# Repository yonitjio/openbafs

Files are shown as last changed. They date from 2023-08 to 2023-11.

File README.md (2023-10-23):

# Basic Automatic Filament Switch

BAFS is a kind of multi material unit for 3d printer. It's very basic, don't expect fancy stuff. It only do one thing: switching filament.

Features:

1. Modular design, i.e. you decide how many ports you want, print accordingly.
2. Only 1 pwm port needed from the printer
3. Redundant design, if one of the motor port stop working, most likely it won't affect the other.
4. Cheap, it uses commonly available parts.
5. Easy to print, for the most parts, you might not need to print with support at all.

BAFS is a great and affordable way to learn and understand how multi filament / multi material 3d printing works.

Be aware this design has the same problems/challenges as similar design using single nozzle and y-splitter: jams, clogging, color bleeds, etc.

To use BAFS you need firmware support, unfortunately, currently there's no official firmware support.

See my other repo for custom firmware:
* Marlin: [openbafs-marlin](https://github.com/yonitjio/openbafs-marlin).
* Klipper: [openbafs-klipper](https://github.com/yonitjio/openbafs-klipper).

Most printers don't have many servo ports, to solve this, I use arduino, stepper motor shield and custom board. There are two variants (branch) regarding communication between printer and bafs:

PWM (Main Branch):
One pwm port from the printer to generate pwm pulse that signal which port to use to external module.

Serial (Sc Branch):
Serial port from the printer to command the external module.

Non printed parts:

- Servos (I use MG996R)
- A Stepper motor (for direct drive printers)
- M5 rod, stainless is preferable.
- M5 to M5 coupler
- M3 bolts and nuts
- M4 bolts
- Long M4 bolts and nuts
- Bearings 625zz, 623zz, u604zz
- Extruder gears
- Grease
- PC4-M6

Electronic parts:

- Arduino
- Protoshield for Arduino
- Stepdown module
- Power Supply
- Connectors
- Wires
- Connectors

These parts are only for the switch, you still need at least a y-splitter. Use whichever work for you. You can search it on thingiverse, printables, etc.

For y-splitter you can try this:
https://www.printables.com/model/488193-4-to-1-bowdenptfe-tube-joinersplitter-stronger-bas

### Extrusion System
Initially BAFS was designed for bowden system, but since I changed my printer to direct drive, I also update BAFS to support direct drive.

With bowden extrusion system, BAFS also acts as the extruder, it uses the printer's stepper motor.

For printers with direct drive extrusion system, it acts as a feeder. It needs additional stepper motor.

Each version requires different firmware. Other than the stepper motor and firmware, everything else is the same.

This repo is for direct drives.

### Electronics
To build the electronics you need to have at least basic skills about arduino and electronics. It requires soldering and making wires with connectors.

It is pretty straight forward. Nothing fancy here. You just need to connect the servos, stepper motor and the printer to arduino.

There are plenty tutorials about using servos and stepper motor with arduino.

Adjust the codes according to your setup.

#### DISCLAIMER:
This is an experimental project. It may or may not work. Use it at your own risk.

#### Notes:
- Even though it's modular, it's better to plan ahead to minimize costs, for example if you plan to use 4 filaments but want to start with 2 first, it's better to prepare the shaft and bolts for 4 filaments from the start. This is because the you need longer shaft and bolts for more ports for the filaments.
- Values in the code are for my setup. Most likely it won't work for yours. Adjust accordingly first.
- If you decided to use this with Klipper, you don't need the software part from this repo.
- Branch SV is for pwm, SC is for serial.
- Refer to [wiki](https://github.com/yonitjio/openbafs/wiki) for more detail.
- If you'd like to buy me a coffee or a tool or supplies for this project, or you want to read more, click here:

  "Buy Me A Coffee" (https://www.buymeacoffee.com/yonitjio)

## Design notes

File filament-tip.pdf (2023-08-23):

Important points in making good filament p:

### 1. Printer Tuning

Tuned printer makes everything easier, at the very least, tuned the e-steps, extrusion mulplier and temperature.

Temperature is the most important factor
Changing the temperature most likely means changing everything else. Use PID or MPC for stable temperature.

Print Temp Tower, choose the lowest possible temp. Usually, it’s easier to make good filament p on lower temp.

### 2. Pressure inside the nozzle

Traveling from print object to wipe toper reduce the pressure inside nozzle. The amount of pressure lost while traveling depends on the distance, ideally this informaon can be calculated and made into formula. I don’t have the skill to do that.

Also, unless the printed model is very simple, most likely the distance/pressure lost varies even between layers on the same object.

Prusa Slicer a.empts to address this with extruding some amount of filament to wipe tower, but somemes it’s not enough.
If necessary, make a straight line on the beginning of the ramming parameter.

### 3. Ramming

The purpose of ramming is to push filament into the nozzle in a way that the melng plasc inside the nozzle isn’t carried away when unloading. Ramming usually requires larger volume than the volume to stabilize pressure.

In other words, we are trying to overwhelm the nozzle melng capabilies, which then, hopefully, when the unloading begins, only the un-melted part of the filament is pulled out.

### 4. Resng

Somemes, it helps to give some resng period. The resng period will allow the filament to melt even more, resulng less string.

### 5. Unloading

Speed plays a big role in making good filament p. Too slow, the effect of ramming is lost. Too fast, the ramming result is not set yet. Both will not produce a good filament p. Start with the default value first (100 mm/s), adjust if needed.

### 6. Cooling

Cooling means that the filament is moved forward and backward for somemes, allowing it to cool down and become hard again. Some filament needs more me to become hard again than other filament.

This is important for Direct Drive system where the filament is parked before the extruder. So: filament will be deformed by the extruder gear which then can cause jamming.

Troubleshoong:

- Thick string / Blunt p
- Not enough me to melt the filament
- Volume too high
- Temperature too low

Soluon:

- Increase the me
- Lower the volumetric speed.
- Increase temperature
- Ripped p
- Unloading speed to fast
- Volume too high

Soluon:

- Lower unloading speed
- lower volumetric speed.
- Smooth, long p
- Not enough volume
- Time is too long
- Temperature too high

Soluon:

- Increase volumetric speed
- Lower me
- Lower temperature
- Use cooling moves
- Inconsistent filament p
- Extruder problem
- Heat creep
- Temperature too high
- Wrong slicer seAng

Soluon:

- Tune the printer
- Check slicer seAngs

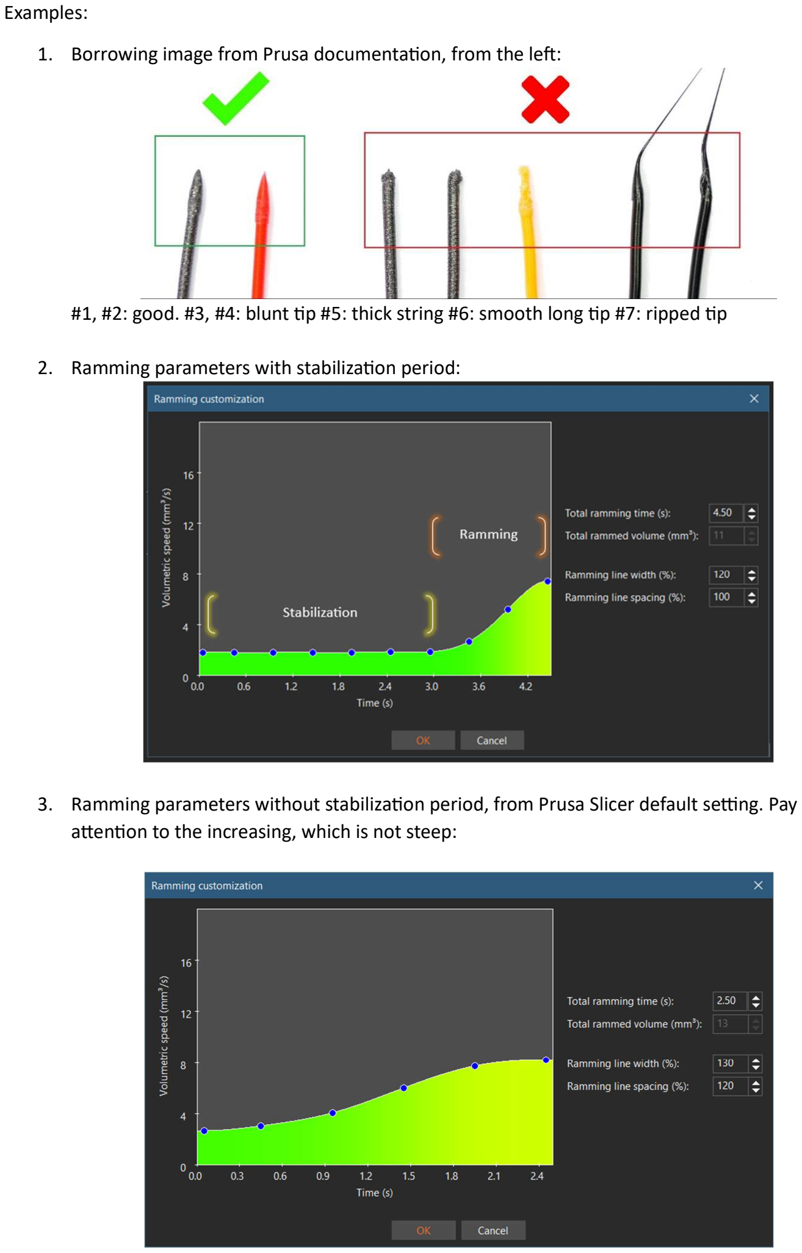
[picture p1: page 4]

Examples:

### 1. Borrowing image from Prusa documentaon, from the le::

#1, #2: good. #3, #4: blunt p #5: thick string #6: smooth long p #7: ripped p

### 2. Ramming parameters with stabilizaon period:

### 3. Ramming parameters without stabilizaon period, from Prusa Slicer default seAng. Pay

a.enon to the increasing, which is not steep:

### 4. Effects of ramming with v6 clone, 0.4 nozzle, 190oC, custom direct drive:

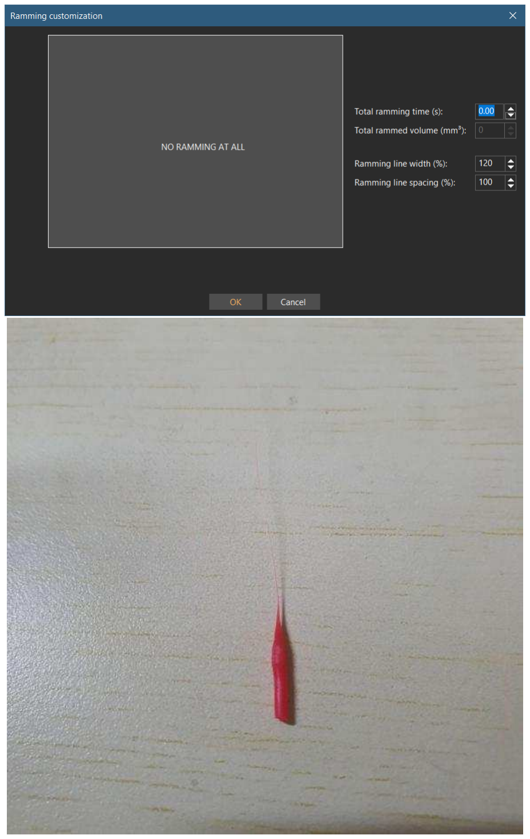
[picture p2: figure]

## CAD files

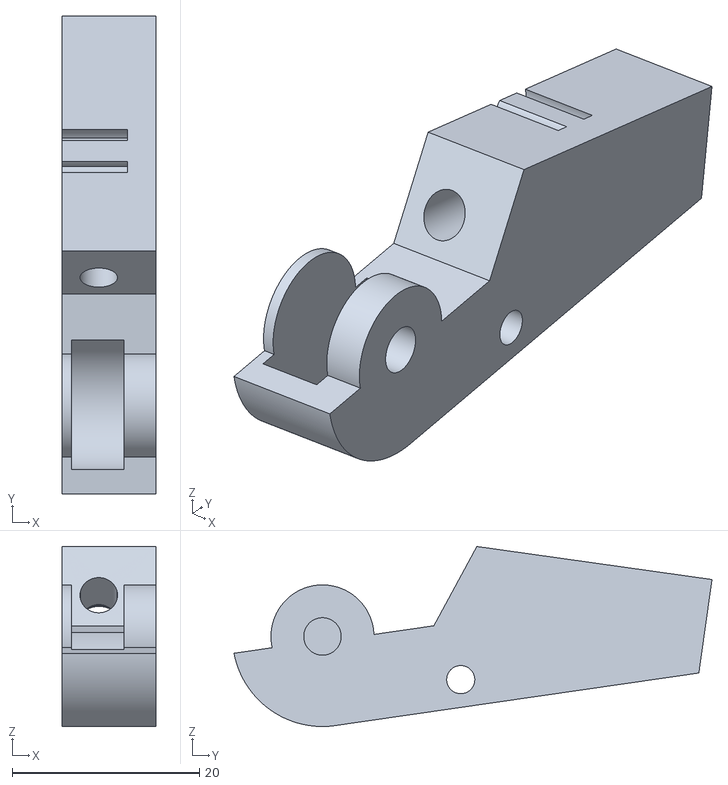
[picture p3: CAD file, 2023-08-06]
prints/Extruder Arm Even.stl
10.0 x 51.0 x 19.2

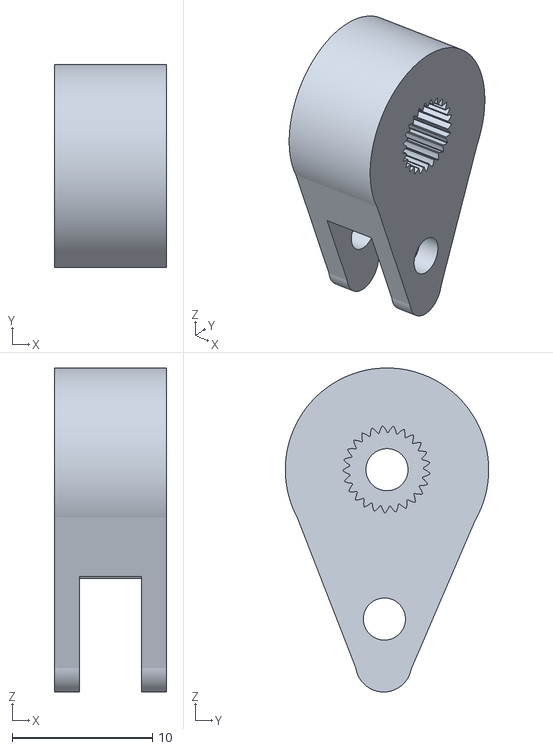
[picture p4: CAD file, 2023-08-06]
prints/Servo Knuckle.stl
8.00 x 14.5 x 23.1

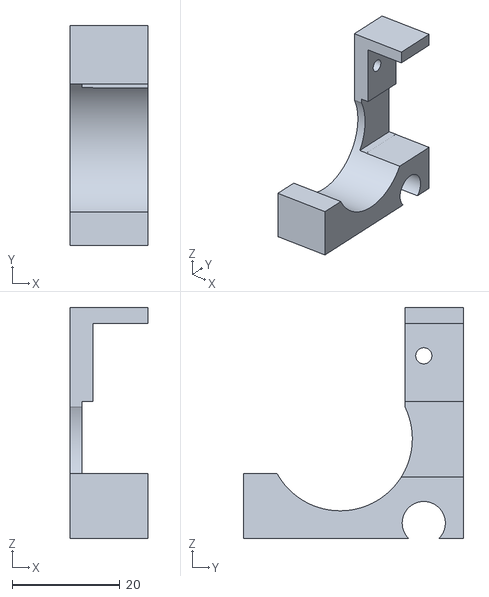
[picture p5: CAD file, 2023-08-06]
prints/Cover Odd.stl
14.4 x 40.8 x 42.9

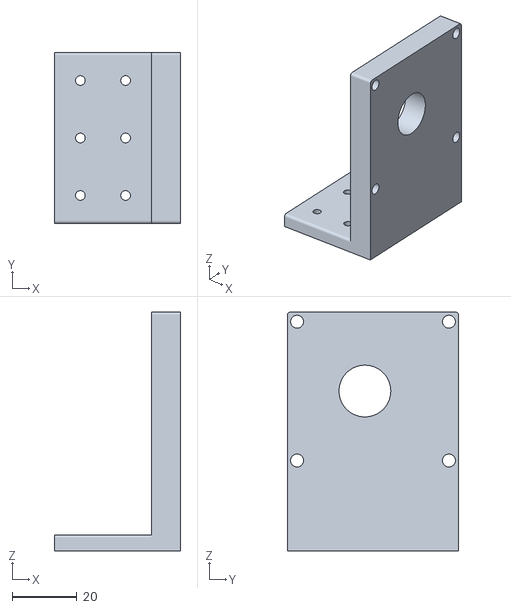
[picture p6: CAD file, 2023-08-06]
prints/End Block.stl
39.0 x 53.0 x 74.0

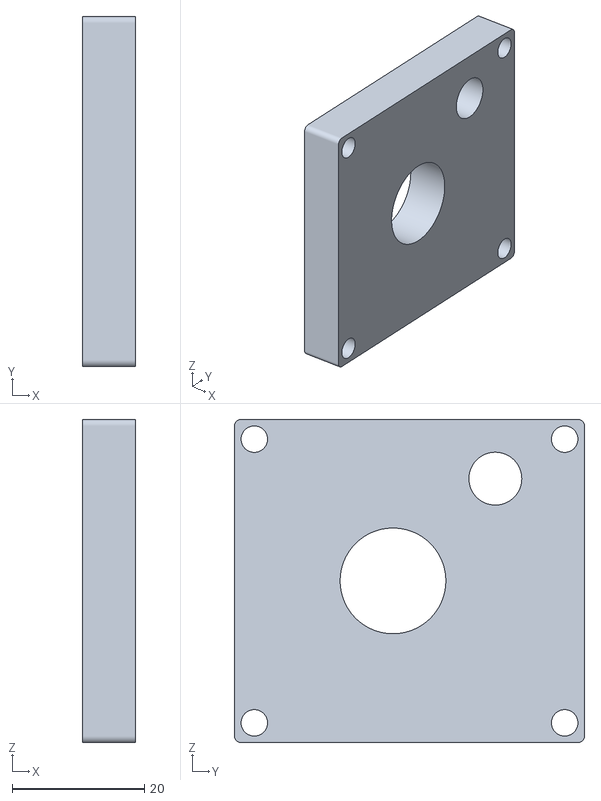
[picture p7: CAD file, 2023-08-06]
prints/Spacer.stl
8.00 x 53.0 x 49.0

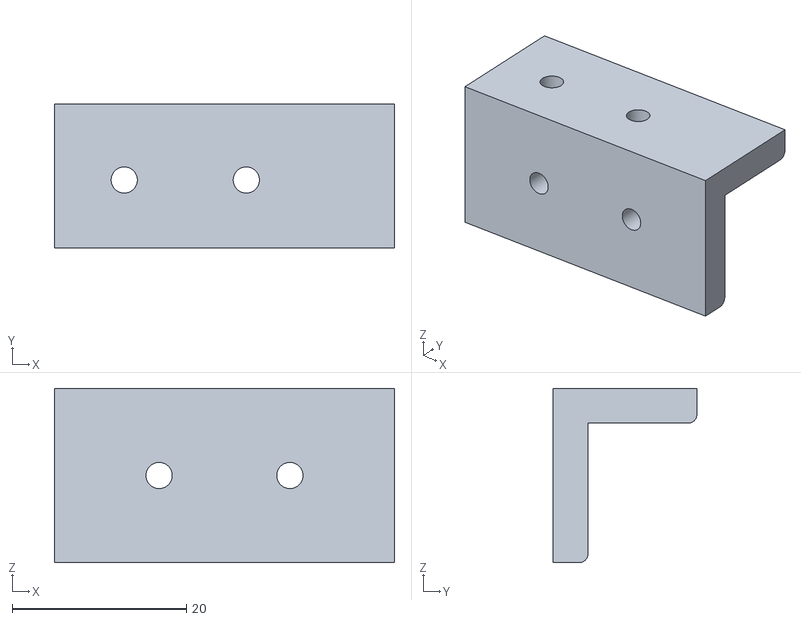
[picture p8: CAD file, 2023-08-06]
prints/End Bracket Bottom.stl
39.0 x 16.5 x 20.0

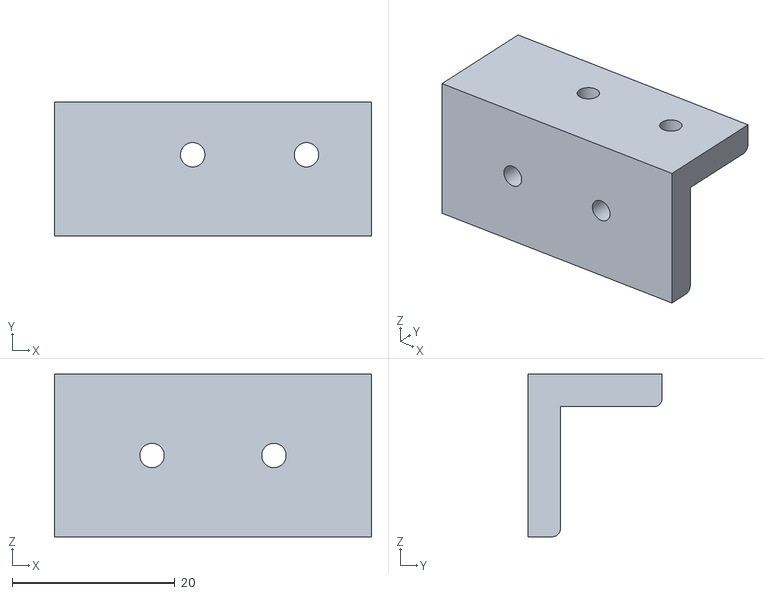
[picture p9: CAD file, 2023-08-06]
prints/Start Bracket Bottom.stl
39.0 x 16.5 x 20.0

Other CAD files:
prints/End Bracket Top.stl
prints/Start Bracket Top.stl
prints/Cover Even.stl
prints/Extruder Arm Odd.stl

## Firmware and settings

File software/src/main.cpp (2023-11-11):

#define SERVOINPUT_SUPPRESS_WARNINGS

#include <SPI.h>
#include <Wire.h>
#include <Adafruit_PWMServoDriver.h>
#include <SoftwareSerial.h>
#include <GCodeParser.h>
#include "Stepper.h"

#define SERVO_CNT 4
#define SERVO_SDA_PIN 4
#define SERVO_SCL_PIN 5
#define SERVO_MIN_MS 600
#define SERVO_MAX_MS 2400
#define SERVO_FREQ 50 // Analog servos run at ~50 Hz updates
#define SERVO_OSC_FREQ 25800000

#define STEPPER_EN_PIN 9
#define STEPPER_STEP_PIN 10
#define STEPPER_DIR_PIN 11
#define SMALL_FEED_DISTANCE 5

// Stepper
const byte micro_step = 16;
const int step_rotation = 200;
const int dist_rotation = 34.56;

const int retract_distance[] = {107, 107, 107, 107};
const int feed_distance[] = {120, 120, 120, 120};
const int slower_margin[] = {10, 10, 10, 10};

float step_accelleration = 40000;
float step_speed = 40000;
float step_max_speed = 40000;
float step_slower_speed = 1000;

// speed is steps/second
// 1.8deg stepper => 200 steps/revolution, 16 microsteps => 3200 steps/rev
// mk8 brass gear diameter => 11mm
// 1 revolution => 34.56mm
// speed 4000 steps/sec => 1000/3200 rev/sec = 0.3125 rev/sec => 0.3125 * 34.56 mm/sec = 10.8 mm/sec
// speed 12000 steps/sec => 12000/3200 = 3.75 rev/sec => 3.75 * 34.56 mm/sec = 129.6 mm/sec

Stepper stepper(AccelStepper::DRIVER, STEPPER_STEP_PIN, STEPPER_DIR_PIN);

// #define DEBUG
// #define DEBUG_SELECTION
#define DEBUG_PRINTER_SERIAL
#define DEBUG_GCODE
// #define DEBUG_STEPPER

// Filament Sensor
#define FILAMENT_SENSOR_PIN 2

// Camera Remote
#define CAM_PIN 3
#define CAM_IDLE 305000
unsigned long cam_last_active = millis();

// Software Serial
#define SERIAL_RX_PIN 12
#define SERIAL_TX_PIN 13

SoftwareSerial printer_serial(SERIAL_RX_PIN, SERIAL_TX_PIN); // RX, TX
GCodeParser GCode = GCodeParser();

int selection = -1;
int last_selection = -1;

int mode = 0; //0: operational, 1: configure, 2: default serial as gcode receiver

// Servo
Adafruit_PWMServoDriver servoController = Adafruit_PWMServoDriver();

const byte servo_on_deg[] = {14, 162, 32, 152};
const byte servo_off_deg[] = {90, 90, 90, 90};

String input_string;

void onRising();
void processPWM();
void switchFilament();
void feedFilament();
String getValue(String data, char separator, int index);
int mapSelection(int s);
int getFeedDistance(int sel);
int getSmallFeedDistance(int sel);
int getSlowerMargin(int sel);
int getRetractDistance(int sel);
void triggerCamera();
void wakeupBluetooth();
void servoWrite(uint8_t i, uint16_t value);
void servoOff(uint8_t i);
void servoOn(uint8_t i);

void setup() {
  Serial.begin(9600);

  // Stepper
  stepper.setEnablePin(STEPPER_EN_PIN);
  stepper.setPinsInverted(true, false, true);
  stepper.setMinPulseWidth(1);

  stepper.setAcceleration(step_accelleration);
  stepper.setMaxSpeed(step_max_speed);
  stepper.setSpeed(step_speed);

  stepper.setMicroStep(micro_step);
  stepper.setDistancePerRotation(dist_rotation);
  stepper.setStepsPerRotation(step_rotation);

  // Servo
  servoController.begin();
  servoController.setOscillatorFrequency(SERVO_OSC_FREQ);
  servoController.setPWMFreq(SERVO_FREQ);
  delay(10);

  // Filament Sensor
  pinMode(FILAMENT_SENSOR_PIN, INPUT_PULLUP);

  // Camera Remote
  pinMode(CAM_PIN, OUTPUT);
  digitalWrite(CAM_PIN, HIGH);
  cam_last_active = millis();

  // Printer Serial
  printer_serial.begin(9600);
  printer_serial.println("Ok");
}

void feedFilament(){
  servoOn(last_selection);
  delay(250);

  stepper.enableOutputs();
  stepper.setCurrentPosition(0);
  stepper.runRelative(getSmallFeedDistance(last_selection));
  stepper.setSpeed(step_speed);
  stepper.disableOutputs();
  delay(250);

  servoOff(last_selection);
  delay(250);
}

void switchFilament(){
  if (selection >= SERVO_CNT) {
    return;
  }

  if (last_selection != selection) {
    if (last_selection > -1) {
      stepper.enableOutputs();

      #ifdef DEBUG_SELECTION
        Serial.print(" Turning on "); Serial.print(last_selection); Serial.println(".");
      #endif

      servoOn(last_selection);
      delay(250);

      #ifdef DEBUG_STEPPER
        Serial.print(" Retracting: ");  Serial.print(last_selection); Serial.print(", "); Serial.print(retract_distance[last_selection]);
      #else
        Serial.print(" Retracting: "); Serial.println(last_selection);
      #endif

      stepper.setCurrentPosition(0);
      stepper.runRelative(-getRetractDistance(last_selection));
      stepper.setSpeed(step_speed);
      delay(250);

      #ifdef DEBUG_SELECTION
        Serial.print(" Turning off "); Serial.print(last_selection); Serial.println(".");
      #endif
      servoOff(last_selection);
      delay(250);

      #ifdef DEBUG_SELECTION
        Serial.print(" Turning on "); Serial.print(selection); Serial.println(".");
      #endif
      servoOn(selection);
      delay(250);

      #ifdef DEBUG_STEPPER
        Serial.print(" Feeding: "); Serial.print(selection); Serial.print(", "); Serial.print(feed_distance[selection]);
      #else
        Serial.print(" Feeding: "); Serial.println(selection);
      #endif

      stepper.setCurrentPosition(0);
      stepper.runRelative(getFeedDistance(selection) - getSlowerMargin(selection));
      stepper.setSpeed(step_slower_speed);
      stepper.runRelative(getSlowerMargin(selection));
      stepper.setSpeed(step_speed);
      delay(250);

      #ifdef DEBUG_SELECTION
        Serial.print(" Turning off "); Serial.print(selection); Serial.println(".");
      #endif

      servoOff(selection);
      delay(250);
    }

    last_selection = selection;

    stepper.disableOutputs();
  }
}

void wakeupBluetooth(){
  digitalWrite(CAM_PIN, LOW);
  delay(50);
  digitalWrite(CAM_PIN, HIGH);
  cam_last_active = millis();
}

void triggerCamera(int d){
  Serial.println("Triggering Camera");
  digitalWrite(CAM_PIN, LOW);
  delay(d);
  digitalWrite(CAM_PIN, HIGH);
  cam_last_active = millis();
}

void processGCode(){
  if (!GCode.blockDelete){
    if (GCode.HasWord('C')) { // C-Codes
      int cCodeNumber = (int)GCode.GetWordValue('C');
      #ifdef DEBUG_GCODE
        Serial.print(" C: "); Serial.print(cCodeNumber); Serial.println(".");
      #endif
      switch (cCodeNumber){
        case 0: { // feed a little bit of filament
          feedFilament();
          if (mode == 0)
            printer_serial.println("ok");
          else
            Serial.println("ok");
        }
        break;
        default: {
            Serial.println(" Unknown C code.");
        }
        break;
      }
    } else if (GCode.HasWord('M')) { // M-Codes
      int mCodeNumber = (int)GCode.GetWordValue('M');
      #ifdef DEBUG_GCODE
        Serial.print(" M: "); Serial.print(mCodeNumber); Serial.println(".");
      #endif
      switch (mCodeNumber){
        case 709: { // Reset
          selection = -1;
          last_selection = -1;
          mode = 0;
          #ifdef DEBUG_GCODE
            Serial.println("BAFSD Reset.");
          #endif
        }
        break;
        case 412: { // Check filament
          int state = digitalRead(FILAMENT_SENSOR_PIN);
          #ifdef DEBUG_GCODE
            Serial.print(" Filament: "); Serial.print(state); Serial.println(".");
          #endif
          if (state == LOW){  // low = filament present, high = filament not present
            if (mode == 0)
              printer_serial.println("ok");
            else
              Serial.println("ok");
          } else {
            if (mode == 0)
              printer_serial.println("no");
            else
              Serial.println("no");
          }
        }
        break;
        case 240: { // Camera
          int duration = (int)GCode.GetWordValue('D');
          triggerCamera(duration);
        }
        break;
        default: {
            Serial.println(" Unknown M code.");
        }
        break;
      }
    } else if (GCode.HasWord('T')) { // T-Codes
      int tCodeNumber = (int)GCode.GetWordValue('T');
      #ifdef DEBUG_GCODE
        Serial.print(" T: "); Serial.print(tCodeNumber); Serial.println(".");
      #endif
      selection = tCodeNumber;
      switchFilament();
      if (mode == 0)
        printer_serial.println("ok");
      else
        Serial.println("ok");
  }
  }
}

void loop() {
  unsigned long now = millis();
  if (now - cam_last_active > CAM_IDLE) {
    wakeupBluetooth();
  }
  if (mode == 0) {
    if (printer_serial.available()) {
      if (GCode.AddCharToLine(printer_serial.read())) {
        #ifdef DEBUG_PRINTER_SERIAL
          Serial.print(" Received: "); Serial.println(GCode.line);
        #endif
        GCode.ParseLine();
        processGCode();
      }
    }
  }
  else if (mode == 2) {
    if (Serial.available()) {
      if (GCode.AddCharToLine(Serial.read())) {
        #ifdef DEBUG_PRINTER_SERIAL
          Serial.print(" Received: "); Serial.println(GCode.line);
        #endif
        GCode.ParseLine();
        processGCode();
      }
    }
    return;
  }

  String command = "";
  if (Serial.available() > 0) {
    String input_string = Serial.readStringUntil('\n');
    input_string.trim();
    Serial.println("Received: " + input_string);
    if (input_string.equalsIgnoreCase("m0")) {
      mode = 0;
      // Servo
      for(int n = 0; n < SERVO_CNT; n++)
      {
        servoOff(n);
        delay(250);
      }
      Serial.println("Entering M0 mode.");
    } else if (input_string.equalsIgnoreCase("m1")) {
      mode = 1;
      Serial.println("Entering M1 mode.");
    } else if (input_string.equalsIgnoreCase("m2")) {
      mode = 2;
      Serial.println("Entering M2 mode.");
    } else if (input_string.equalsIgnoreCase("rs")) {

      double pulselength;
      pulselength = 1000000; // 1,000,000 us per second

      uint16_t prescale = servoController.readPrescale();

      prescale += 1;
      pulselength *= prescale;
      pulselength /= SERVO_OSC_FREQ;

      uint16_t pwm = servoController.getPWM(selection);
      uint16_t pulse = pwm * pulselength;

      unsigned long camIdle = millis() - cam_last_active;

      Serial.print(" Mode: "); Serial.println(mode);
      Serial.print(" Selection: "); Serial.println(selection);
      Serial.print(" pwm: "); Serial.println(pwm);
      Serial.print(" pulse: "); Serial.println(pulse);
      Serial.print(" pulseLength: "); Serial.println(pulselength);
      Serial.print(" Cam Idle: "); Serial.println(camIdle);

      if (pulse < SERVO_MIN_MS) {
        pulse = SERVO_MIN_MS;
      }

      if (pulse > SERVO_MAX_MS) {
        pulse = SERVO_MAX_MS;
      }
      uint16_t deg = map(pulse, SERVO_MIN_MS, SERVO_MAX_MS, 0, 180);

      Serial.print(" deg: "); Serial.println(deg);
      Serial.print(" filament: "); Serial.println(digitalRead(FILAMENT_SENSOR_PIN));
      Serial.println();
    }else {
      command = input_string;
    }
  }
  if (mode == 1) {
    if (command.length() > 0){
      #ifdef DEBUG
        Serial.print("command: "); Serial.println(command);
      #endif

      char cmd = getValue(command, ' ', 0)[0];
      String p1 = getValue(command, ' ', 1);
      String p2 = getValue(command, ' ', 2);

      switch (cmd)
      {
        case 'c': // camera
          {
            int d_val = p1.toInt();
            triggerCamera(d_val);
          }
        break;
        case 'e': // small feed
          {
            long t = millis();
            feedFilament();
            t = millis() - t;
            Serial.print("time: "); Serial.println(t);
          }
          break;
        case 'f': // switch filament p1 selection
          {
            long t = millis();
            selection = p1.toInt();
            switchFilament();
            t = millis() - t;
            Serial.print("time: "); Serial.println(t);
          }
          break;
        case 'd': // move stepper p1 = steps
          {
            long step_val = p1.toInt();

            #ifdef DEBUG
              Serial.print("step_val: "); Serial.println(p1);
            #endif

            stepper.enableOutputs();
            stepper.move(step_val);
            stepper.runToPosition();
            stepper.setSpeed(step_speed);
            stepper.disableOutputs();
          }
          break;
        case 'p': // move stepper p1 = distance, p2 = not used
          {
            long dis_val = p1.toInt();
            long t = millis();
            #ifdef DEBUG
              Serial.print("dis_val: "); Serial.println(p1);
            #endif

            stepper.enableOutputs();
            stepper.setCurrentPosition(0);
            #ifdef DEBUG
              long steps = stepper.runRelative(dis_val);
            #else
              stepper.runRelative(dis_val);
            #endif
            stepper.setSpeed(step_speed);
            stepper.disableOutputs();

            t = millis() - t;
            #ifdef DEBUG
              Serial.print("steps: "); Serial.println(steps);
              Serial.print("time: "); Serial.println(t);
            #endif
          }
          break;
        case 'm': // select servo p1 = servo
          {
            int s_val = p1.toInt();

            #ifdef DEBUG
              Serial.print("s_val: "); Serial.println(p1);
            #endif

            s_val = constrain(s_val, 0, SERVO_CNT);
            last_selection = s_val;
            selection = s_val;
          }
          break;
        case 's': // set servo degree p1 = servo index, p2 = degree
          {
            int s_val = p1.toInt();
            int d_val = p2.toInt();

            #ifdef DEBUG
              Serial.print("s_val: "); Serial.print(p1); Serial.print( " d_val: "); Serial.println(p2);
            #endif

            s_val = constrain(s_val, 0, SERVO_CNT);
            d_val = constrain(d_val, 0, 180);

            Serial.print("Moving "); Serial.println(s_val);
            servoWrite(s_val, d_val);
          }
          break;
        case 't': // test servos and stepper
          {
              for(int n = 0; n < SERVO_CNT; n++)
              {
                servoWrite(n, 100);
                delay(500);
                servoOff(n);
                delay(250);
              }

              stepper.enableOutputs();
              stepper.setCurrentPosition(0);
              stepper.runRelative(100);
              stepper.setSpeed(step_speed);
              stepper.disableOutputs();

          }
          break;
        case 'z': // tests
          {
              for(int n = 0; n < SERVO_CNT; n++)
              {
                servoWrite(n, 100);
                delay(500);
                servoOff(n);
                delay(250);
              }

              stepper.enableOutputs();
              stepper.setCurrentPosition(0);
              stepper.runRelative(100);
              stepper.setSpeed(step_speed);
              stepper.disableOutputs();

          }
          break;
        default:
          break;
      }
      command = "";
    }
  }
}

String getValue(String data, char separator, int index)
{
    int maxIndex = data.length() - 1;
    int j = 0;
    String chunkVal = "";

    for (int i = 0; i <= maxIndex && j <= index; i++)
    {
        chunkVal.concat(data[i]);

        if (data[i] == separator)
        {
            j++;

            if (j > index)
            {
                chunkVal.trim();
                return chunkVal;
            }

            chunkVal = "";
        }
        else if ((i == maxIndex) && (j < index)) {
            chunkVal = "";
            return chunkVal;
        }
    }

    return chunkVal;
}

int getRetractDistance(int sel) {
  if (sel % 2 == 0) {
    return retract_distance[sel];
  } else {
    return -retract_distance[sel];
  }
}

int getSmallFeedDistance(int sel) {
  if (sel % 2 == 0) {
    return SMALL_FEED_DISTANCE;
  } else {
    return -SMALL_FEED_DISTANCE;
  }
}

int getFeedDistance(int sel) {
  if (sel % 2 == 0) {
    return feed_distance[sel];
  } else {
    return -feed_distance[sel];
  }
}

int getSlowerMargin(int sel) {
  if (sel % 2 == 0) {
    return slower_margin[sel];
  } else {
    return -slower_margin[sel];
  }
}

void servoWrite(uint8_t i, uint16_t value)
{
  if(value < SERVO_MIN_MS)
  {  // treat values less than 544 as angles in degrees (valid values in microseconds are handled as microseconds)
    if(value < 0) value = 0;
    if(value > 180) value = 180;
    value = map(value, 0, 180, SERVO_MIN_MS,  SERVO_MAX_MS);
  }
  servoController.writeMicroseconds(i, value);
}

void servoOn(uint8_t i)
{
  servoWrite(i, servo_on_deg[i]);
}

void servoOff(uint8_t i)
{
  servoWrite(i, servo_off_deg[i]);
  delay(250);
  servoController.setPWM(i, 0, 0);
}

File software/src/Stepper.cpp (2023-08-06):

#include "Stepper.h"

Stepper::Stepper(
	uint8_t interface, 
	uint8_t pin1, 
	uint8_t pin2, 
	uint8_t pin3, 
	uint8_t pin4, 
	bool enable) : 
	AccelStepper(interface, pin1, pin2, pin3, pin4, enable) {} 

/**
 * Set the microSteps value.
 * @param value
 */
void Stepper::setMicroStep(int value) {
	microSteps = value;
}

/**
 * Set the number of steps a step motor should do to complete one full rotation.
 * @param value
 */
void Stepper::setStepsPerRotation(int value) {
	stepsPerRotation = value;
}

/**
 * Set the distance which the step motor cover with one full rotation.
 * @param value
 */
void Stepper::setDistancePerRotation(float value) {
	distancePerRotation = value;
}

/**
 * Return the current distance from the origin.
 * @return
 */
float Stepper::getCurrentPositionDistance() {
	return currentPosition() / (microSteps * stepsPerRotation / distancePerRotation);
}

/**
 * The motor travel a certain distance.
 * @param value
 */
long Stepper::moveToDistance(float value) {
  long steps = value * microSteps * stepsPerRotation / distancePerRotation;
  moveTo(steps);
  return steps;
}

/**
 * Move the motor to a new relative distance.
 * @param value
 */
long Stepper::moveRelative(float value)
{
  long steps = value * microSteps * stepsPerRotation / distancePerRotation;
  move(steps);
  return steps;
}

/**
 * Move and run the motor to a new relative distance.
 * @param value
 */
long Stepper::runRelative(float value)
{
  long steps = value * microSteps * stepsPerRotation / distancePerRotation;
  move(steps);
  runToPosition();
  return steps;
}

/**
 * The motor goes to the new specified distance.
 * @param value
 */
long Stepper::runToNewDistance(float value) {
    long steps = moveToDistance(value);
    runToPosition();
	return steps;
}

/**
 * Set the angle per rotation property.
 * @param value
 */
void Stepper::setAnglePerRotation(float value) {
	anglePerRotation = value;
}

/**
 * The motor goes to the new specified angle.
 * @param value
 */
void Stepper::moveToAngle(float value) {
	moveTo(value * microSteps * stepsPerRotation / anglePerRotation);
}

/**
 * The motor goes to the new specified angle.
 * @param value
 */
void Stepper::runToNewAngle(float value) {
    moveToAngle(value);
    runToPosition();
}

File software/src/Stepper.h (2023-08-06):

#ifndef Stepper_h
#define Stepper_h

#include <AccelStepper.h>

class Stepper : public AccelStepper {
    private:
		int microSteps = 16;
		int stepsPerRotation = 200;
		float distancePerRotation = 34.56;
		float anglePerRotation = 360;
		/*
		ts = microsteps * stepsperrotation = 360 = 34.55752 mm
		1 degree = degreeperrotation / 360
		1 step = stepsperrotation / 360
		1 mm = distanceperrotation / 360
		steps = distance * stepperrotation / distanceperrotation				
		*/

    public:
		Stepper(
			uint8_t interface = AccelStepper::DRIVER, 
			uint8_t pin1 = 2, 
			uint8_t pin2 = 3, 
			uint8_t pin3 = 4, 
			uint8_t pin4 = 5, 
			bool enable = true);

		void setMicroStep(int value);

		void setStepsPerRotation(int value);

		void setDistancePerRotation(float value);

		float getCurrentPositionDistance();

		long moveToDistance(float value);

        long moveRelative(float value);
    
        long runRelative(float value);

		long runToNewDistance(float value);

		void setAnglePerRotation(float value);

		void moveToAngle(float value);

		void runToNewAngle(float value);
};

#endif

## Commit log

2023-08-18 Change of behavior when starting a print
    - Custom gcode M709. This will reset bafs. Use this at the start of a print.
    - Change of behavior, now bafs will ignore first toolchange gcode. This is to address inconsistent behavior of slicer which may or may not issue toolchange at the start of a print. Consequently, for every print, you need to prepare the starting filament so it's ready to print, i.e. loaded to nozzle.
    [main.cpp]
2023-08-30 Integration with Tiny FIlament Sensor
2023-09-26 Add serial communication support and fix typo
    [main.cpp]
2023-10-23 Purge Bucket, Splitter and Wiki
2023-11-11 Update gcodes for filament tip shaping with silicon pad
2023-11-11 Migrate to Nano and Fix timeout with camera shutter
    [main.cpp]
